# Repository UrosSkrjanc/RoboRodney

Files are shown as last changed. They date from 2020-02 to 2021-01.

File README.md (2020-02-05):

# RoboRodney

Zdravo.

Tuakj lahko snamete vse potrebno za izdelavo in sestavljanje robota.

V direktoriju Navodila so vsa navodila za sestavljanje, inštaliranje in uproabo robota. 

V direktoriju Nacrti co datoteke STL za tiskanje delov robota.

Direktorij roborodney pa vsebuje ROS paket za uproavljanje robota

uros.skrjanc@gmail.com

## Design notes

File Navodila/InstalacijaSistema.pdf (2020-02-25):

Kratek postopek inštalacije
1. Uvod
2. Formatiranje SD kartice, kopiranje sistema na kartico in namestitev sistema
3. Prijava uporabnika root kot glavnega uporabnika
4. Povezovanje uporabnika na robota
5. Nameščanje popravkov
6. SWAP datoteka
7. Dodajanje dodatnega I2C vodila
8. Nastavitve mreže
9. Inštalacija ROS
10. Inštalacija WiringPi
11. Prevajanje paketov
12. Preklapljanje med okenskim in terminalskim vmesnikom

### 1 – UVOD

Navodilo za inštalacijo se nanaša na operacijski sistem Ubuntu Mate 18.04 in ROS Melodic Morenia distribucijo. Pri ostalih operacijskih sistemih so podrobnosti lahko drugačne.

Programi za formatiranje in namestitev sistema na micro SD kartice delujeta na Windows operacijskih sistemih, PuTTY in FileZila pa tudi na nekaterih drugih operacijskih sistemih. Več informacij lahko dobite na straneh https://www.putty.org/ in https://filezilla-project.org/. Seveda se za terminalski dostop do robota in urejanje datotek lahko uporablja tudi druge programe, odvisno od operacijskega sistema, ki ga uporabljate na računalniku.

Sistem se nahaja na naslovu https://ubuntu-mate.org/download/, ROS distribucija pa na naslovu http://wiki.ros.org/melodic.

Za morebitne nejasnosti pri inštalaciji sem na voljo preko elektronske pošte: uros.skrjanc@gmail.com. V skladu s svojimi zmožnostmi in pristojnostmi bom skušal na vprašanja čim bolj jasno in enostavno odgovoriti.

### 2 – FORMATIRANJE SD KARTICE, KOPIRANJE SISTEMA NA KARTICO IN NAMESTITEV SISTEMA

Najprej s programom SD Card Formatter, ki ga dobimo na naslovu https://www.sdcard.org/downloads/formatter/, formatiramo micro SD kartico. Kapaciteta kartice naj bo najmanj 16GB, še bolje pa je, če je kapaciteta kartice 32GB. Nastavitve pri formatiranju kartice so privzete.

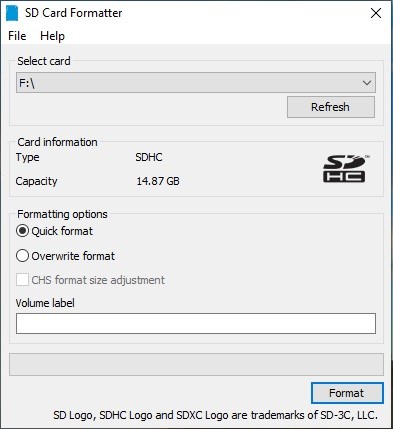
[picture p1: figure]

Z interneta prenesite sliko operacijskega sistema Ubuntu Mate 18.04.2. Ta se nahaja na https://ubuntu-mate.org/download/. Izberete verzijo za Raspberry Pi ARMv7.

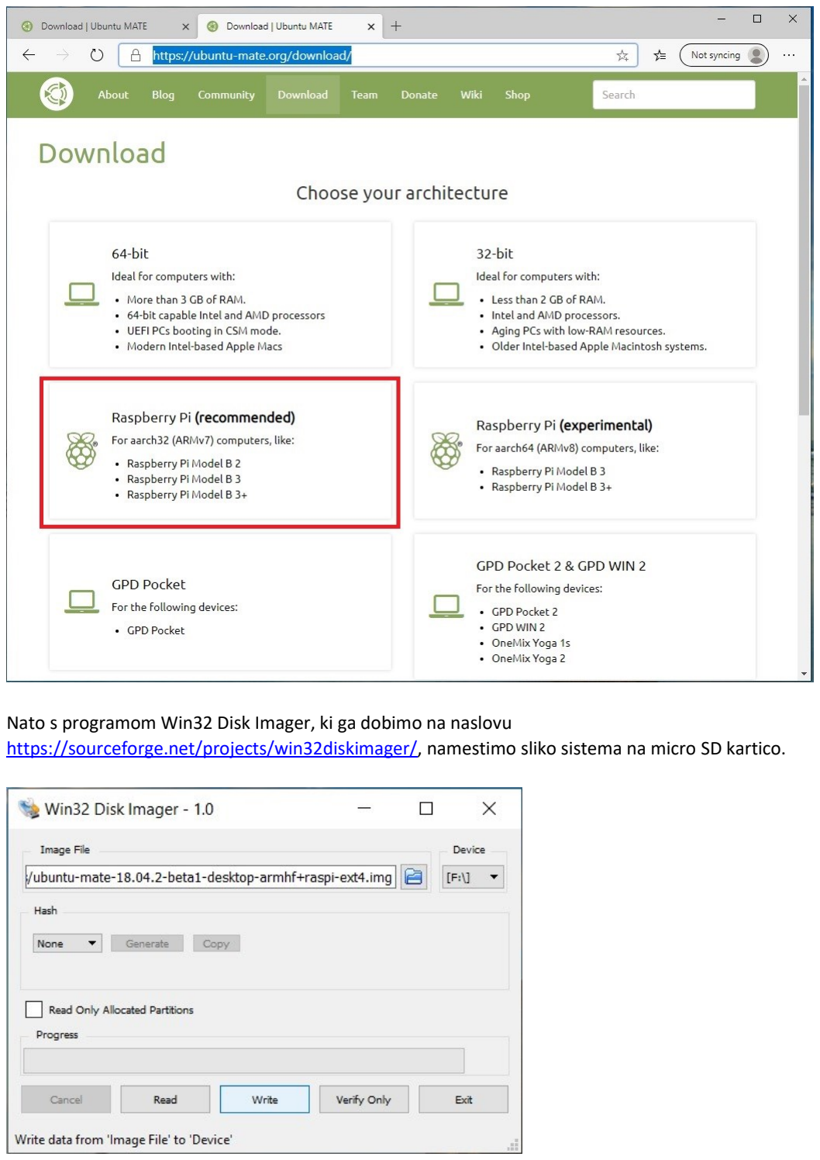
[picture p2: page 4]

Nato s programom Win32 Disk Imager, ki ga dobimo na naslovu https://sourceforge.net/projects/win32diskimager/, namestimo sliko sistema na micro SD kartico.

Inštalacija je preprosta, najbolje je, da je Raspberry računalnik z UTP kablom priklopljen na internet, tako da zazna datum, uro ter lokalne nastavitve. Glede na to, da je večina navodil za urejanje nastavitev operacijskega sistema na internetu napisana v angleščini, je za lažje delo najbolje, da osnovni jezik sistema ostane angleščina, tipkovnica pa se nastavi na slovensko.

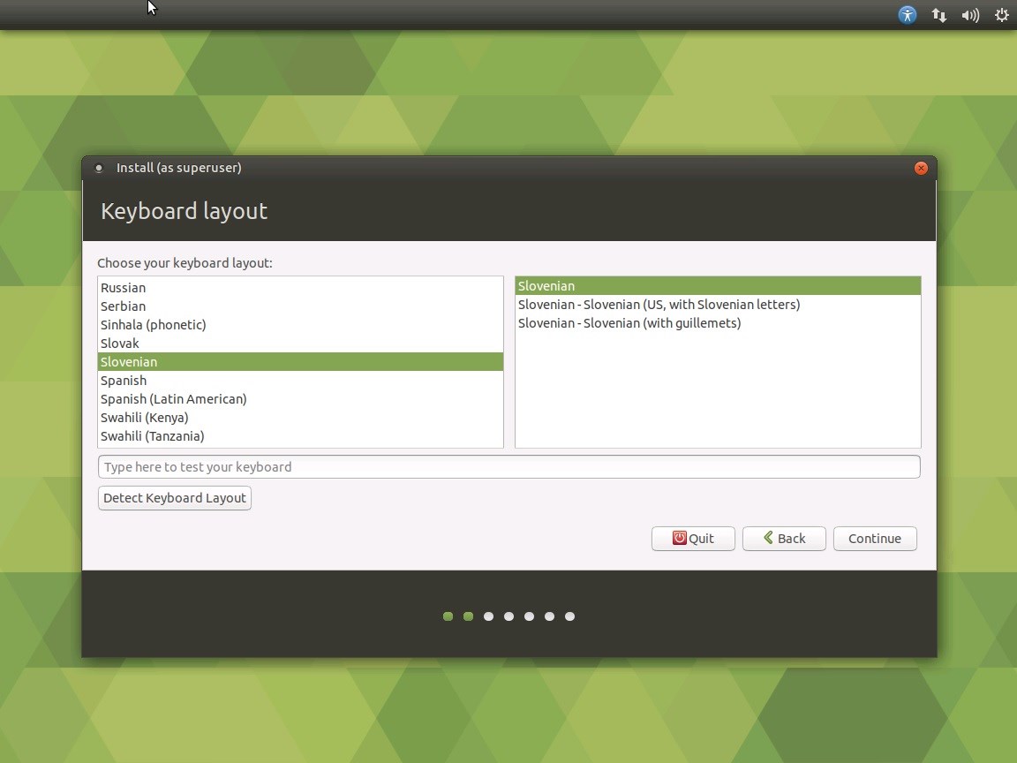
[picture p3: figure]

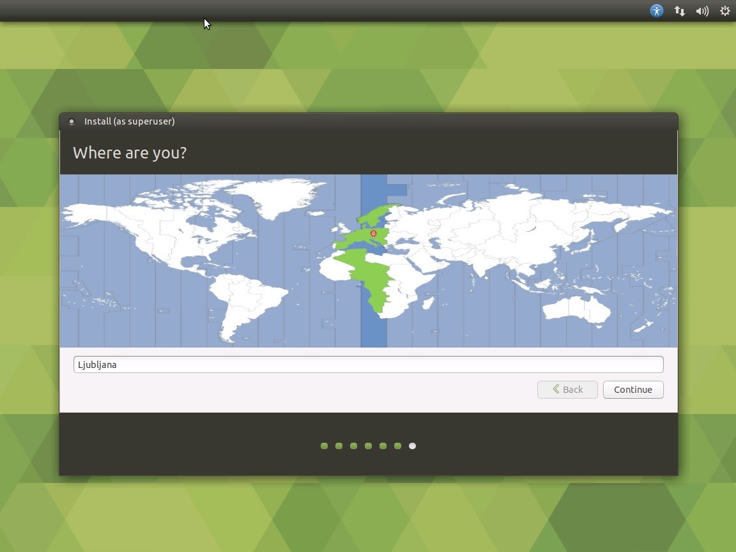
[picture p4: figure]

Uporabniško ime in geslo lahko izberete poljubno. Zaradi bolj enostavnega poganjanja je priporočljivo, da se uporabnik prijavi avtomatsko.

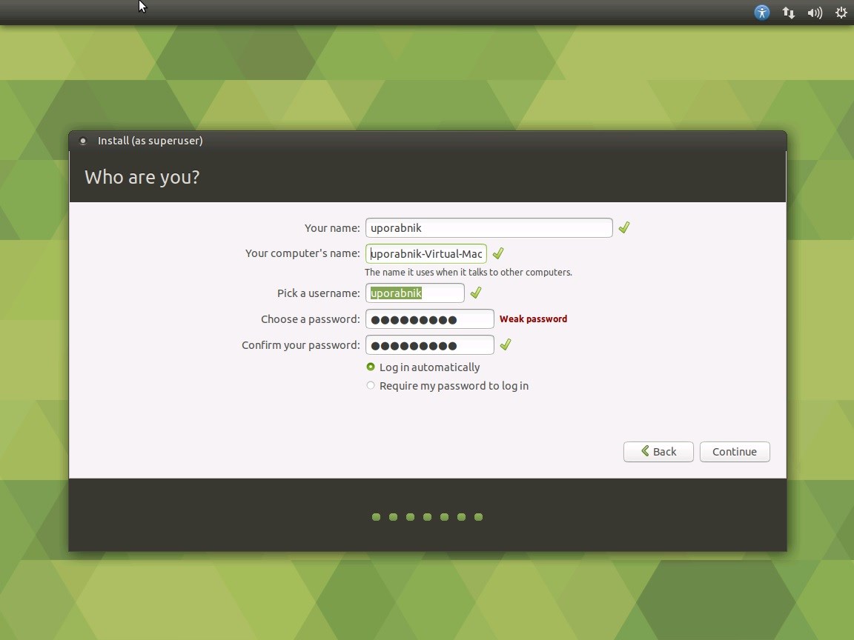
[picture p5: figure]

Ker SSH protokol na Ubuntu 18.04 ob inštalaciji ne deluje pravilno, je potrebna njegova ponovna namestitev. To naredimo tako, da odpremo terminalsko okno, v meniju (Menu – System tool – MATE Terminal) in poženemo naslednje ukaze:
sudo apt-get remove openssh-server
sudo apt-get purge openssh-server
sudo apt-get install openssh-server

Nato omogočimo še uporabo kamere in vodila I2C. To naredimo tako, da odpremo terminalsko okno v meniju (Menu – System tool – MATE Terminal) in poženemo program za konfiguracijo Raspberry računalnika.
Ukaz:
sudo raspi-config
Potem izberemo možnosti:
- Interfacing options – Camera – Yes
- Interfacing options – I2C – Yes

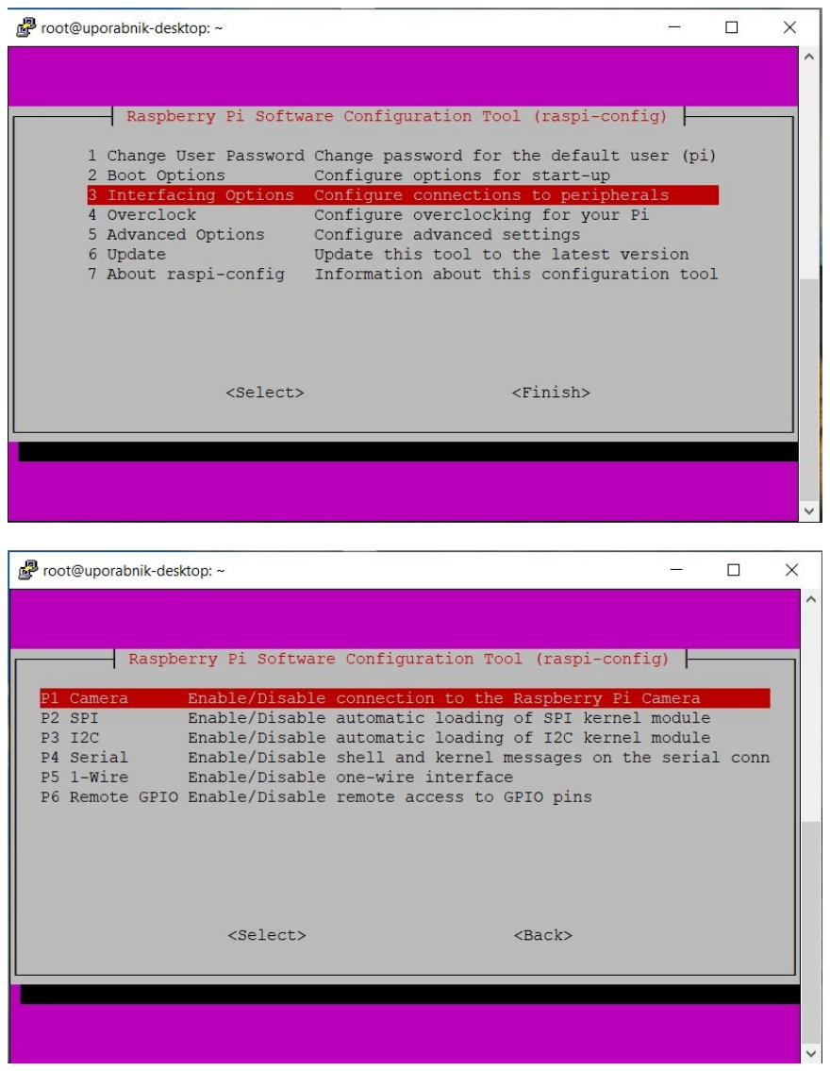
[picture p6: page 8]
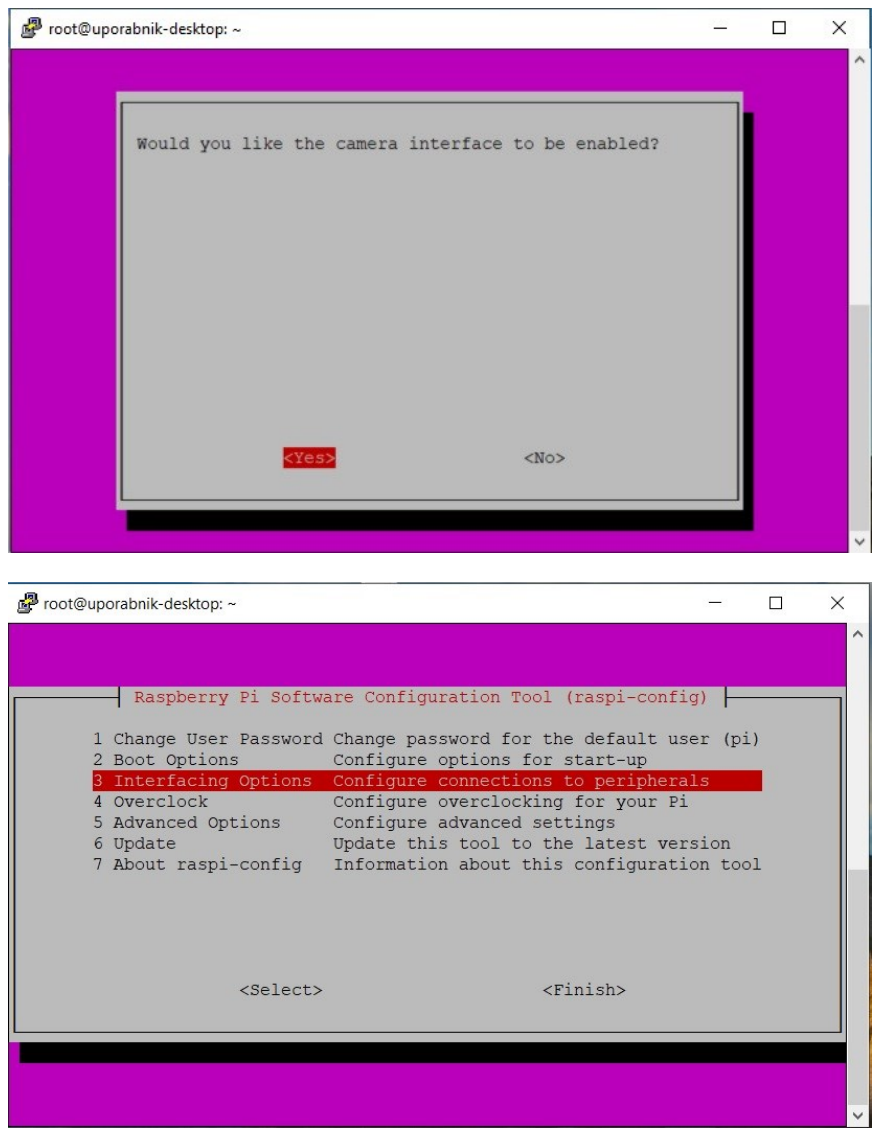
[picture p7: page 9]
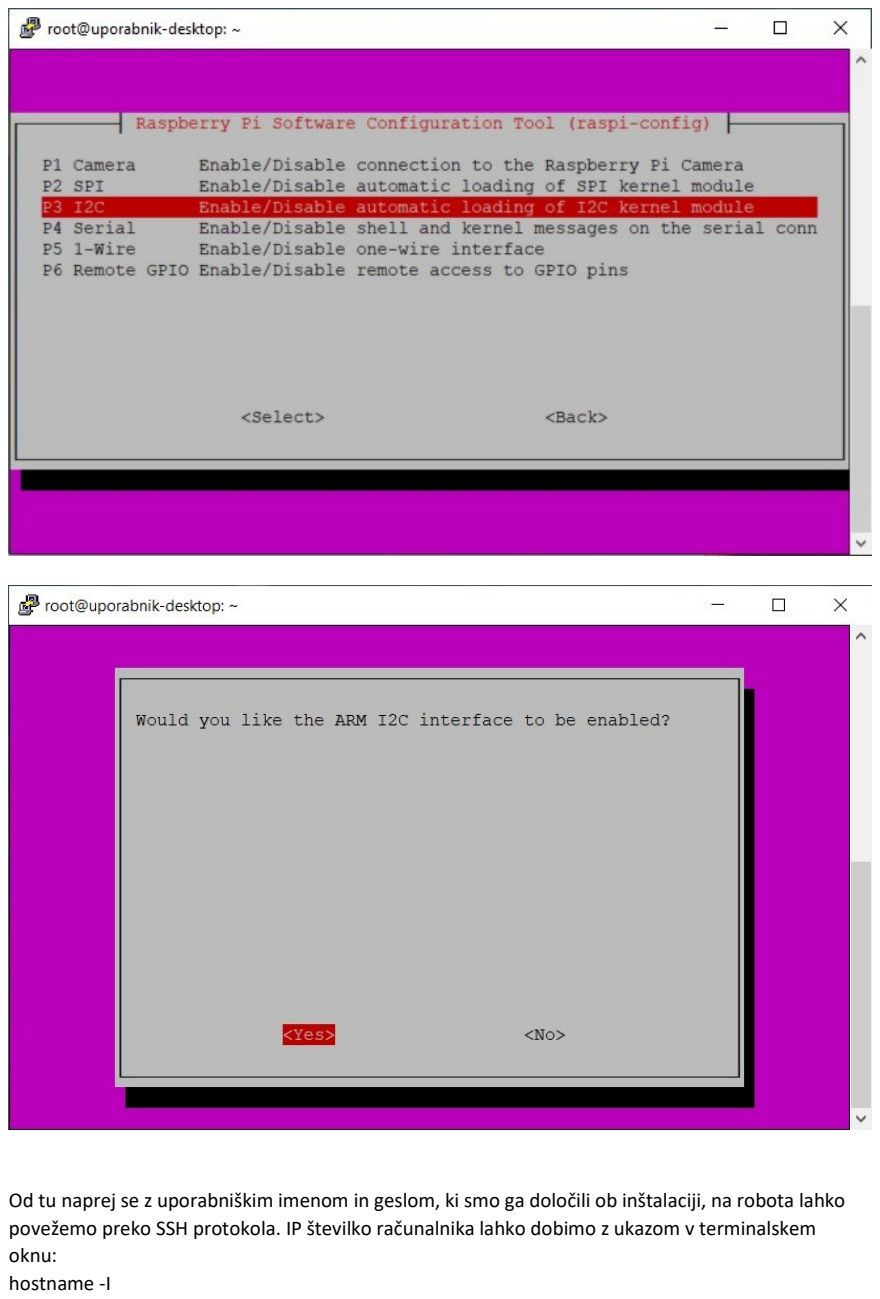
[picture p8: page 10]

Od tu naprej se z uporabniškim imenom in geslom, ki smo ga določili ob inštalaciji, na robota lahko povežemo preko SSH protokola. IP številko računalnika lahko dobimo z ukazom v terminalskem oknu:
hostname -I

Pred nadaljnjim delom je priporočljivo ponovno pognati robota. To lahko naredimo z ukazom v terminalskem oknu:
sudo shutdown -r now

### 3 - PRIJAVA UPORABNIKA ROOT KOT GLAVNEGA UPORABNIKA

Čeprav načeloma ni priporočljivo, da se uporabnik v računalnik prijavlja kot glavni administratorski račun, dostop do servo motorja zahteva prav to. Najprej moramo spremeniti geslo administratorskega računa. Poženemo ukaz za spremembo gesla, vpišemo najprej svoje geslo, potem pa dvakrat novo administratorsko geslo.
Ukaz:
sudo passwd root

Administratorskemu računu je potrebno dovoliti tudi logiranje preko SSH protokola. To dosežemo tako, da v datoteki /etc/ssh/sshd_config vrstico
# PermitRootLogin prohibit-password

spremenimo v
PermutRootLogin yes

Nato ponovno poženemo robota: sudo shutdown -r now

### 4 - POVEZOVANJE UPORABNIKA NA ROBOTA

Na robota se lahko povežem preko Putty programa z ukazno vrstico, datoteke pa lahko urejamo s programom FileZilla.

Programe lahko dobimo na naslovih:
Putty - https://www.putty.org/
FileZilla - https://filezilla-project.org/

Putty je namenjen povezavi preko SSH protokola na oddaljen računalnik in poganjanju ukazov v terminalskem načinu. Najprej na robotu z ukazom hostname -I preverim IP številko robota, potem odprem program in v okence vtipkam število, nakar program vpraša za uporabniško ime in geslo. Vpišemo uporabnika root in geslo, ki smo ga določili administratorskemu računu. Če so podatki vpisani pravilno in če je SSH dostop na robotu omogočen, potem se odpre terminal, preko katerega lahko krmilimo robota.

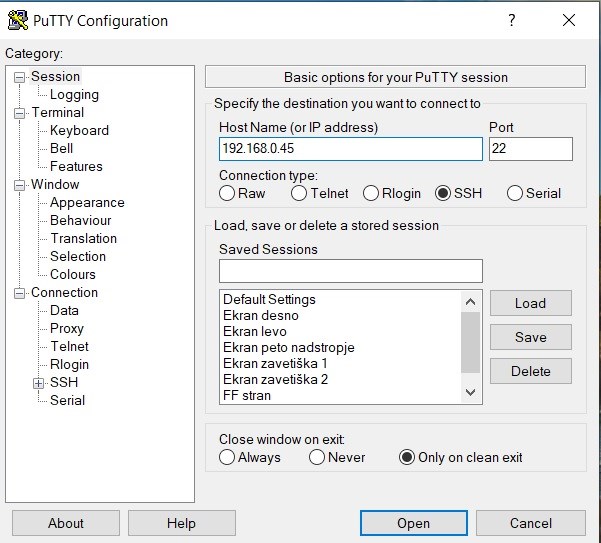
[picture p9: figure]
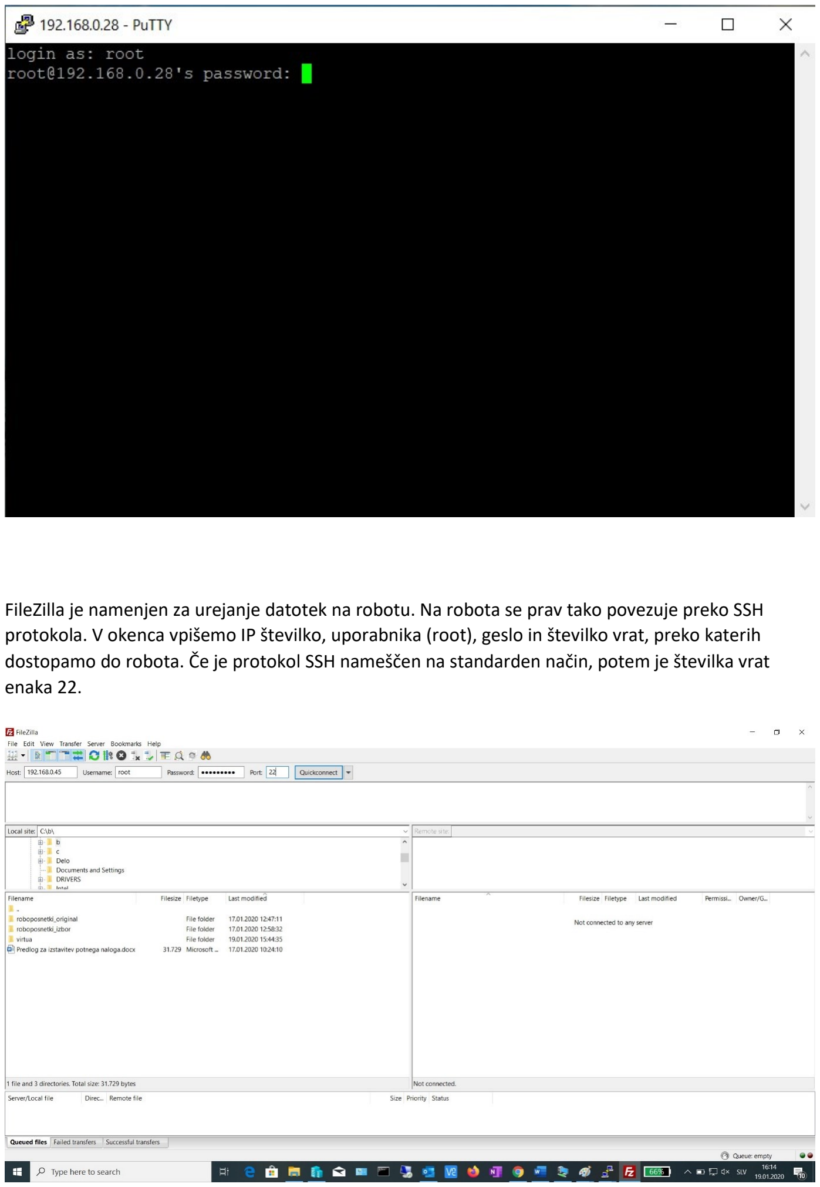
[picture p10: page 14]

FileZilla je namenjen za urejanje datotek na robotu. Na robota se prav tako povezuje preko SSH protokola. V okenca vpišemo IP številko, uporabnika (root), geslo in številko vrat, preko katerih dostopamo do robota. Če je protokol SSH nameščen na standarden način, potem je številka vrat enaka 22.

### 5 - NAMEŠČANJE POPRAVKOV

Na robota se preko SSH protokola povežem kot root uporabnik in izvedem naslednje ukaze apt-get update
apt-get upgrade

Včasih pri inštalaciji sistem opozori, da kakega nameščenega programa ne potrebuje več. V tem primeru poženemo ukaz za odstranitev teh programov:
apt-get autoremove

Naštete ukaze po potrebi izvedemo večkrat. Vsekakor tolikokrat, da so nameščeni vsi potrebni programi.

Pri inštalaciji sistema lahko pride do naslednje napake:
Errors were encountered while processing: /var/cache/apt/archives/linux-firmware-raspi2_1.20190819-0ubuntu0.18.04.1_armhf.deb

Za nadaljnjo inštalacijo je potrebno pognati ukaz:
dpkg -i --force-all /var/cache/apt/archives/linux-firmware-raspi2_1.20190819-0ubuntu0.18.04.1_armhf.deb

Samo ime datoteke, ki je ne more procesirati, se lahko razlikuje, tako da v ukazu uporabite ime datoteke, ki vam jo vrne.

Za pravilno delovanje robota moramo namestiti še:
knjižnico za I2C vodilo
apt-get install libi2c-dev
knjižnico zbar za zaznavanje QR kode:
apt-get install zbar-tools libzbar-dev libzbar0
knjižnico za komunikacijo z PS3 kompatibilno konzolo: apt-get install libusb-dev joystick python-pygame bluetooth in knjižnico za zajem slike s kamere v pythonu:
apt install python3-pip
pip3 install picamera

Da kamera na Ubuntu 18.04 deluje pravilno, je potrebno na koncu datoteke /etc/modules dodati vrstico bcm2835-v4l2.
Ukaz:
sudo echo bcm2835-v4l2 >> /etc/modules

### 6 - SWAP DATOTEKA

Pred namestitvijo ROS-a je priporočljivo narediti še swap datoteko. To naredimo z naslednjimi ukazi sudo fallocate -l 2G /swapfile
sudo chmod 600 /swapfile
sudo mkswap /swapfile
sudo swapon /swapfile
echo '/swapfile none swap sw 0 0' | sudo tee -a /etc/fstab

Če swap datoteka že obstaja in je premajhna, je potrebno najprej z datoteke /etc/fstab izbrisati vrstico, ki definira swap datoteko, potem pa izvesti zgoraj navedene korake.

Ukaz za odpiranje /etc/fstab datoteke:
sudo nano /etc/fstab

Zbrišemo vrstico
/swapfile | none | swap sw | 0 0

Nato ponovno zaženemo računalnik in izvedemo zgornje vrstice.

Če je swap datoteka pravilno kreirana, preverimo z ukazom free –m

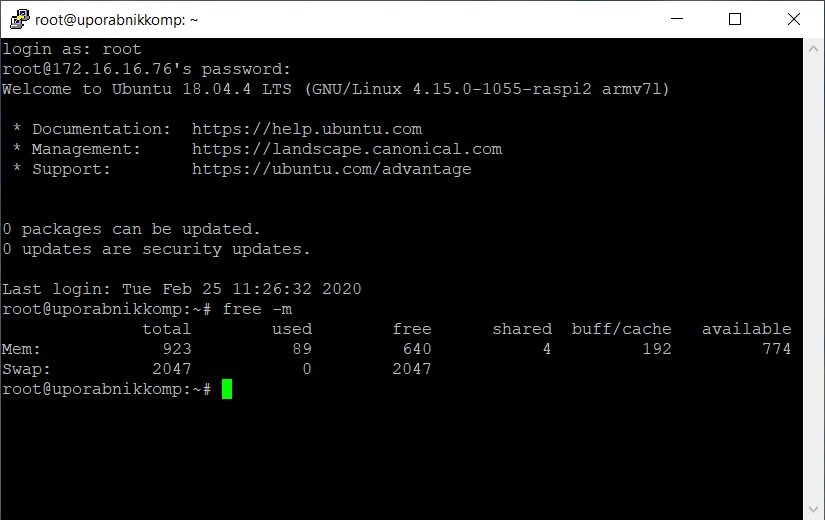
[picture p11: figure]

### 7 - DODAJANJE I2C VODILA

Pri komponentah, ki sem jih izbral za robota, imata laserski senzor VL53L0X in senzor za orientacijo v prostoru BNO055 isti naslov, zato je potrebno dati senzorja na različna I2C vodila. VL53L0X na robotu je nameščen na I2C številka 1, BNO055 pa na številki 3. Laser je na standardnem, privzetem vodilu oz. pinih (SDA-GPIO02, SCL-GPIO03), BNO055 pa je povezan s pini SDA-GPIO20, SCL-GPIO21. Zato moram v datoteko /boot/config.txt vpisati naslednjo vrstico: dtoverlay=i2c-gpio,bus=3,i2c_gpio_delay_us=1,i2c_gpio_sda=27,i2c_gpio_scl=22

Datoteko je potrebno spreminjati preko terminalskega okna. Spremembo izvedemo z ukazom: sudo echo dtoverlay=i2c-gpio,bus=3,i2c_gpio_delay_us=1,i2c_gpio_sda=27,i2c_gpio_scl=22 >> /boot/config.txt

Oznake pinov se nanašajo na spodnjo sliko:

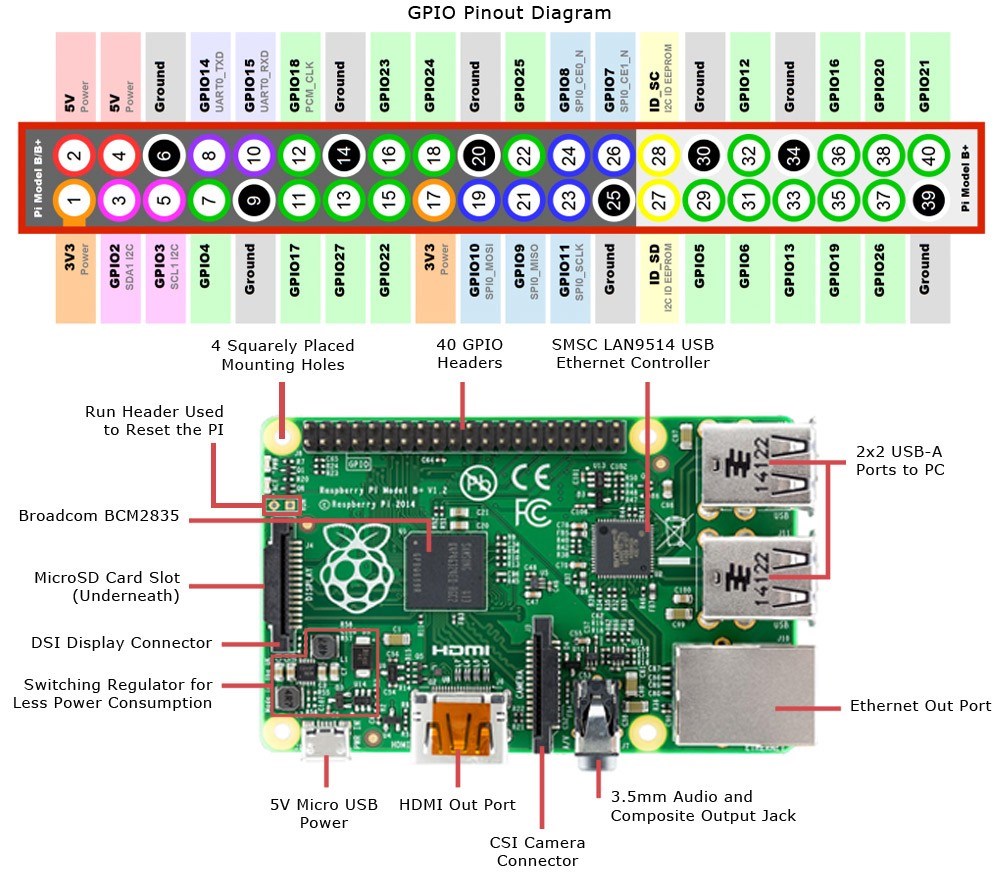
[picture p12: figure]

### 8 - NASTAVITVE MREŽE

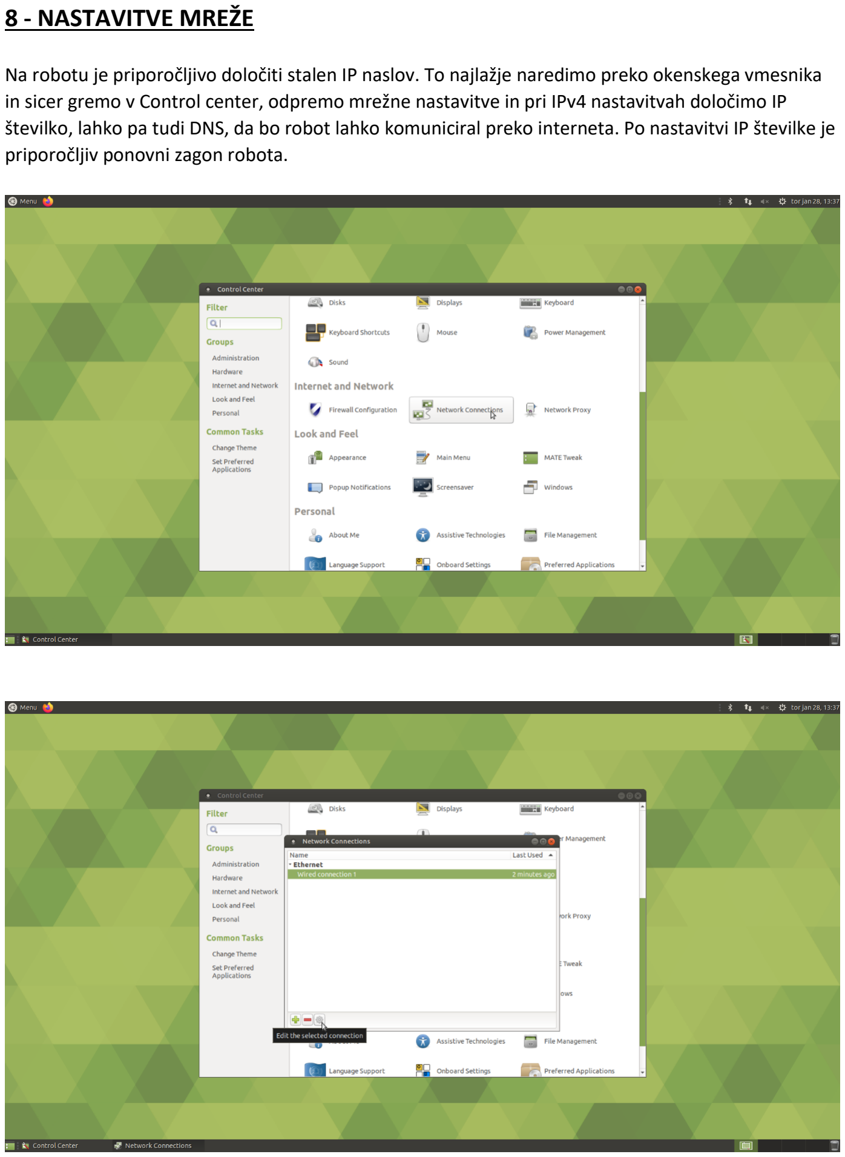
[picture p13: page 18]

Na robotu je priporočljivo določiti stalen IP naslov. To najlažje naredimo preko okenskega vmesnika in sicer gremo v Control center, odpremo mrežne nastavitve in pri IPv4 nastavitvah določimo IP številko, lahko pa tudi DNS, da bo robot lahko komuniciral preko interneta. Po nastavitvi IP številke je priporočljiv ponovni zagon robota.

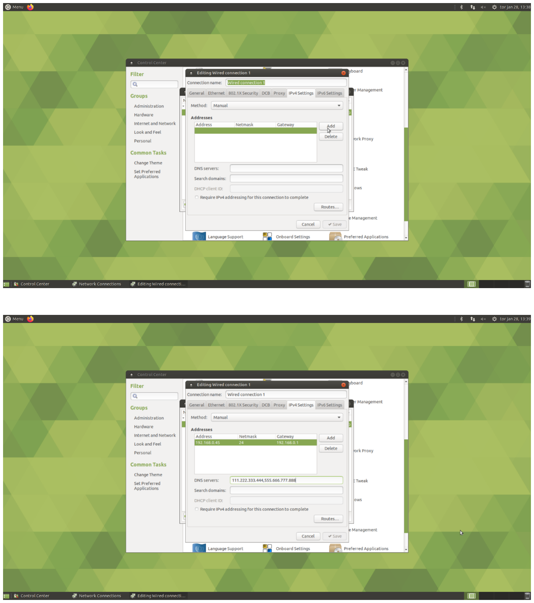
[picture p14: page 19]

### 9 - INŠTALACIJA ROS

Za prevajanje in poganjanje programov za nadzor robota je potrebno namestiti ROS distribucijo. Programi so preizkušeni na ROS Melodic Morenia distribuciji, z majhnimi popravki pa lahko delujejo tudi na drugih distribucijah.

Distribucija se nahaja na strani http://wiki.ros.org/Distributions.

Navodila za namestitev se nahajajo na strani http://wiki.ros.org/melodic/Installation/Ubuntu.

Ukazi za namestitev ROS Melodic Morenia:
sudo sh -c 'echo "deb http://packages.ros.org/ros/ubuntu $(lsb_release -sc) main" > /etc/apt/sources.list.d/ros-latest.list'
sudo apt-key adv --keyserver 'hkp://keyserver.ubuntu.com:80' --recv-key C1CF6E31E6BADE8868B172B4F42ED6FBAB17C654
sudo apt update
sudo apt install ros-melodic-desktop-full
sudo rosdep init
rosdep update
echo "source /opt/ros/melodic/setup.bash" >> ~/.bashrc
sudo apt install python-rosinstall python-rosinstall-generator python-wstool build-essential source ~/.bashrc

Potrebno je narediti še delovni prostor (workspace), v katerem bodo tekli programi. Namesto imena rosmelodic lahko izberete tudi kako drugo ime.

Ukazi za kreiranje delovnega prostora:
mkdir rosmelodic
cd rosmelodic
mkdir src
catkin_make

Nato v datoteko bashrc dodam vrstico source /root/rosmelodic/devel/setup.bash Ukaz:
echo "source /root/rosmelodic/devel/setup.bash " >> ~/.bashrc

Za delovanje PS3 kompatibilne konzole je potrebno namestiti tudi paket joy za ROS Ukaz:
apt-get install ros-melodic-joy
apt-get install ros-melodic-joystick-drivers

### 10 – INŠTALACIJA WIRINGIP

Za delovanje elektro motorjev je potrebno namestiti tudi knjižnico WiringPi. Navodila za namestitev se nahajajo na strani http://wiringpi.com/download-and-install/

Ko se povežete na robota preko terminalskega načina, izvedete naslednje ukaze:
git clone git://github.com/WiringPi/WiringPi.git
cd WiringPi
./build

Če pri prevajanju prihaja do napak, poskusite izvesti še naslednje korake: cd gpio
rm *.o
cd ..
./build

Knjižnico lahko prenesete na računalnik tudi z naslova https://github.com/WiringPi/WiringPi

### 11 – PREVAJANJE PAKETOV

Ko sta operacijski sistem in ROS distribucija uspešno nameščeni, je čas, da prenesete paket programov za robota, ga prevedete ter preizkusite delovanje robota.

Paket za navigacijo robota se nahaja na naslovu https://github.com/UrosSkrjanc/RoboRodney. Paket je v imeniku roborodney.

Najprej je potrebno programe prenesti v delovni prostor, ki smo ga kreirali v koraku 9. Preko terminalnega vmesnika se povežite na robota, nato pa izvedite naslednje ukaze:
git clone https://github.com/UrosSkrjanc/RoboRodney
cd RoboRodney
cp -r roborodney /root/rosmelodic/src

Nato se lahko lotite prevajanja paketov cd /root/rosmelodic
catkin_make

Samo prevajanje naj bi potekalo brez težav. Lahko se prikažejo določena opozorila, a na samo prevajanje programov in delovanje robota to ne vpliva. Ko se programi prevedejo pravilno, je robot pripravljen za uporabo.

### 12 – PREKLAPLJANJE MED OKENSKIM IN TERMINALSKIM VMESNIKOM

Ker ima računalnik Raspberry Pi 3B+ samo 1GB pomnilnika, bi lahko okenski vmesnik robotazaradi velike porabe pomnilnika pri delovanju oviral, zato je na koncu inštalacije in pred uporabo robota priporočljivo vklopiti zagon robota v terminalskem načinu. To storimo tako, da se na robota povežemo preko terminalskega okna in poženemo ukaz raspi-config. Izberemo možnost Boot options, nato možnost Desktop/CLI in Console Text console. Možnost potrdimo z OK. Ko izberemo izhod iz nastavitev, nas vpraša, če še enkrat zaženemo računalnik. Možnost izberemo in robot bi se moral zagnati v tekstovnem načinu.

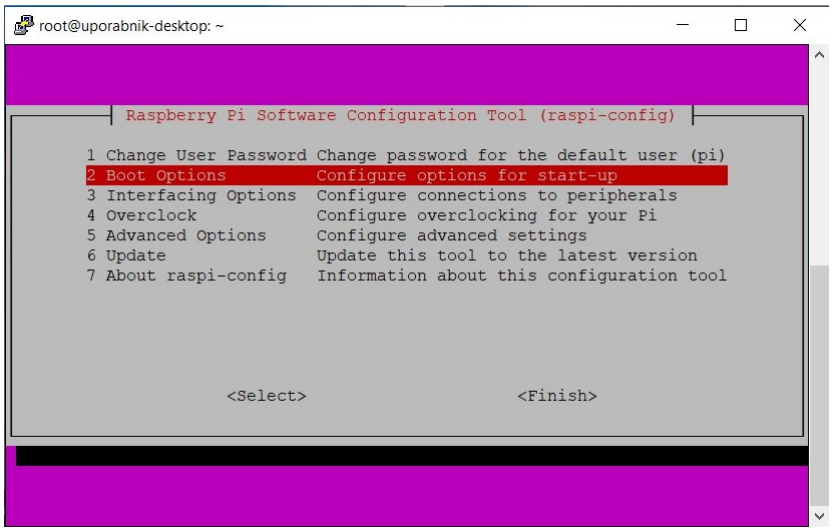
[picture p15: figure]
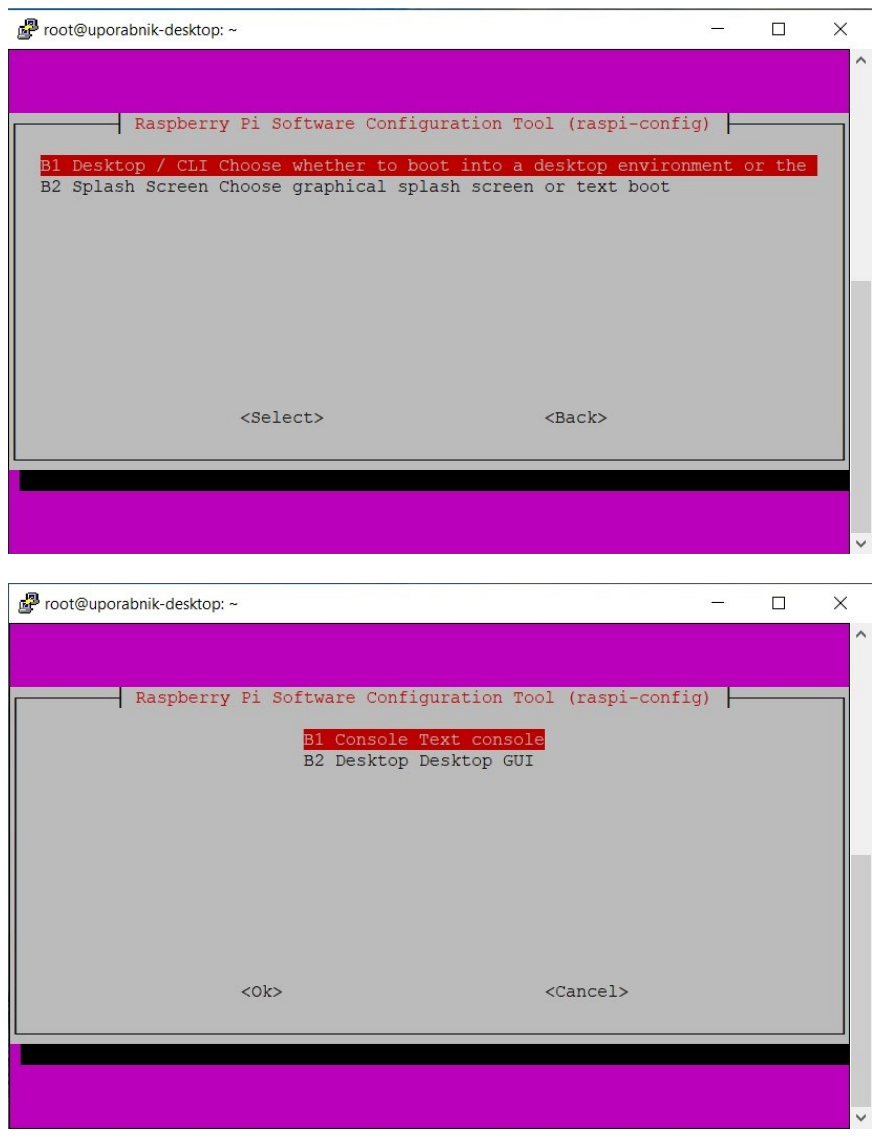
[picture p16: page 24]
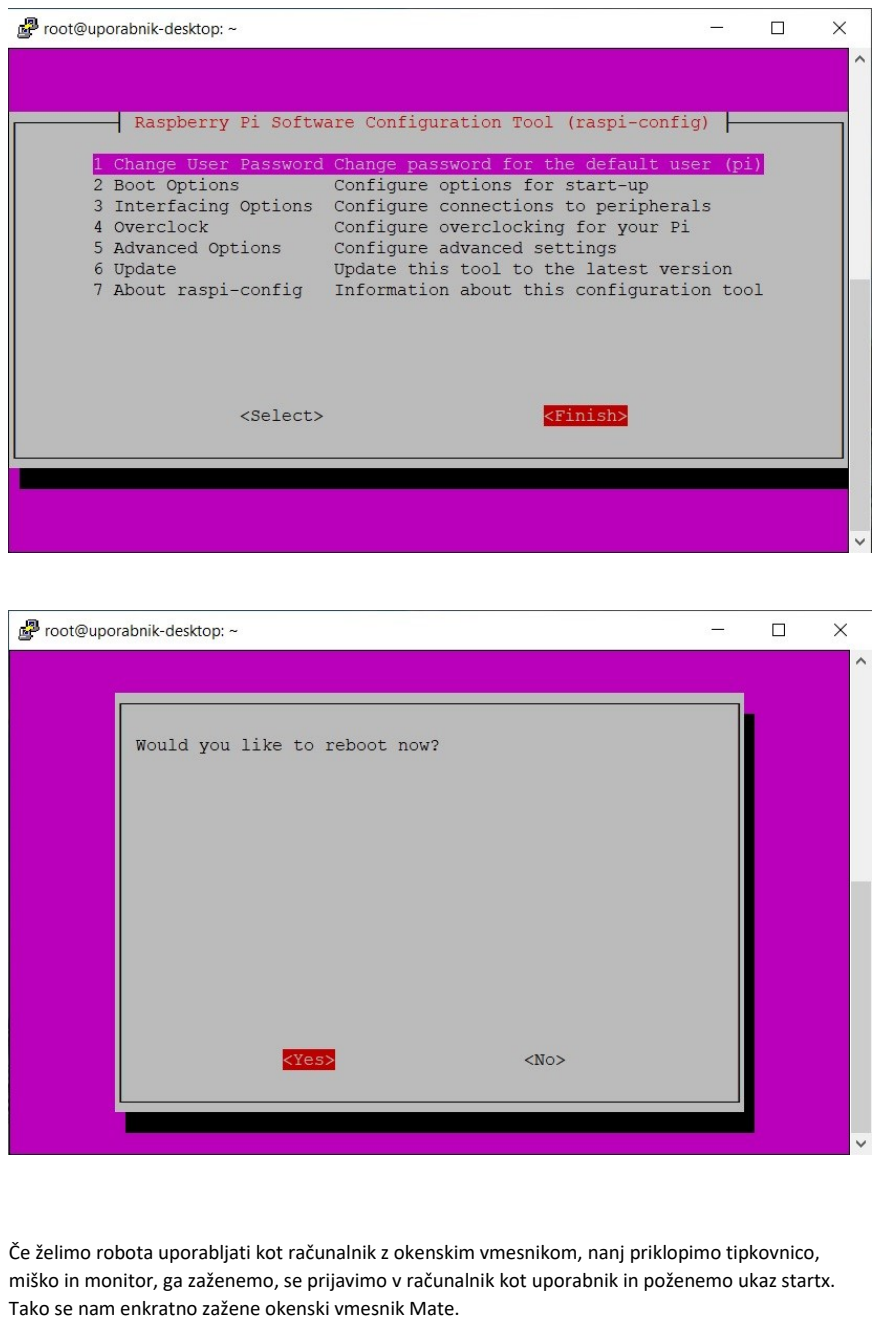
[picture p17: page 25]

Če želimo robota uporabljati kot računalnik z okenskim vmesnikom, nanj priklopimo tipkovnico, miško in monitor, ga zaženemo, se prijavimo v računalnik kot uporabnik in poženemo ukaz startx. Tako se nam enkratno zažene okenski vmesnik Mate.

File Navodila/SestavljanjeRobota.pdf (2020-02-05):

POTROŠNIKI ELEKTRIKE
Laser
Bno055
RTC (opcijsko)
Ultrasonic (opcijsko)
Servo motor

RPI ima 2x 5V in 2x3.3V
1x 5V je vhod z baterij
1x 5V je izhod na servo motor
Bi moral narediti kabel, ki ga priklopim na 3,3V izhod in GND, ima pa štiri izhode na naprave. Na obeh straneh je ženski priključek

Za robota potrebujem
Rdeč in bel kabel za ubec-RPI
5x rdeč in bel kanel za naprave, te kable zlotat za štiri naprave Rdeč in bel kabel za servo motor
Vsi napajalni kabli so M-Ž

Naprave na zgornji plasti (laser, ultrasonic, BNO055) bom napajal preko kabla, ki sem ga naredil iz več kablov
Za servo potegnem 5V kabel z RPI
RTC dobi napajanje z drugega 3.3V izhoda na RPI

SPODNJI DEL

Sestavni deli
- Plastično ohišje spodnji del
- Raspberry Pi 3B+
- Micro SD kattica 32GB
- Motor driver
- UBEC
- 4x motorji
- 4x kolesa
- Priključek za baterije
- 8 kablov moški-moški
- 4 kabli moški-ženska

Najprej na zgornjo stran ohišja z vijaki in maticami pričvrstim Raspberry Pi 3B+ in motor driver in sicer tako, da v vsako luknjo potisnem vijak, na vsak vijak potem dam dve matici, zato da RPI in motor driver nista direktno pričvrščena na plastiko, namestim RPI in motor driver na ohišje in ju spodaj pričvrstim z matico. Matice med RPI in plastiko ter med motor driver in plastiko dam zato, da se na dotika direktno plastike in da se ne segreva. Da ima zračenje.

SLIKA

Na motor driver priklopim UBEC in nastavek za baterije, potem pa z UBECA priklopim kabla na RPI, da ima napajanje. To naredim na 5V vhod in GND. Preizkusim še delovanje tako, da priklopim na RPI monitor, tipkovnico in miško ter poženem računalnik. Če se RPI postavi in deluje, so žice povezane pravilno. Rdeč kabel iz UBEC-a povežem na fizični pin 4, črni kabel oz. ozemljitev pa na fizični pin 6.

Postopek je tak, da vzamem M-Ž črn in bel kabel. Oba kabla na ženskem delu priklopim na UBEC, na moškem delu pa odstranim plastiko ter priklopim na motor-driver na vtiča 4(+) in 5(-), zraven teh kablov dam še prikjuček za baterije – rdeč je +, črn je -. Potem vzamem še črn in bel M-Ž kabel in moški del obeh kablov priklopim na UBEC, ženski pa na RPI in sicer bel kabel na fizični pin 4, črn kabel pa na fizični pin 6. Bel kabel je +, črn pa -.

Nato vzamem štiri motorje in osem kablov M-M. Kablom snamem plastično ohišje in rahlo zvijem pine, tako da se nekako zahaklajo na motor SLIKA!!! Potem pine kablov še bolj zvijem in spajkam kable na motor. Ko so žičke spajkane na motor, motorje namestim na ohišje, vsakega z dvema M3 30mm vijakoma in maticama, tako, da so vsi motorji na isti višini. Žičke potegnem skozi velike luknje ob straneh ohišja ter jih s spodnje strani potegnem do motor-driverja. Žičke naj bodo vsaka svoje barve, tako da jih je potem lažje priklopiti na motor-driver. Del žičke, ki ga namestim v motor driver, z izolirnim trakom izoliram, da se žičke nasprotnih polov ne dotikajo drug drugih. Plastiko z žičke snamem zato, ker je plastika prevelika in je težko pravilno namestiti žičke na motor driver.

SLIKE!!!!

Kable z motorjev potem potegnem skozi luknjo na sredini ohišja in jih namestim v motor driver.

Ko sem priklopil pine GPIO6, GPIO 13, GPIO 19 in GPIO 26, sta desna motorja pričela delovati takoj, ko sem priklopil baterije.

Motorji imajo + in – tako, kot je na sliki. To je pomembno zato, da pravilno priklopim kable na motor driver.

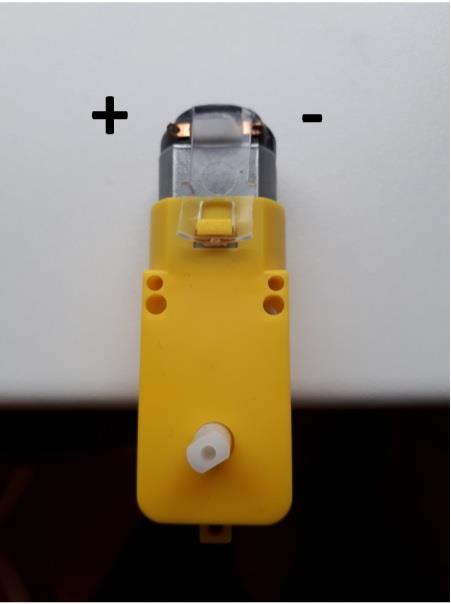
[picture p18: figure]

Pri motor driverju so pomembni tisti priklopi, ki so označeni z bold.

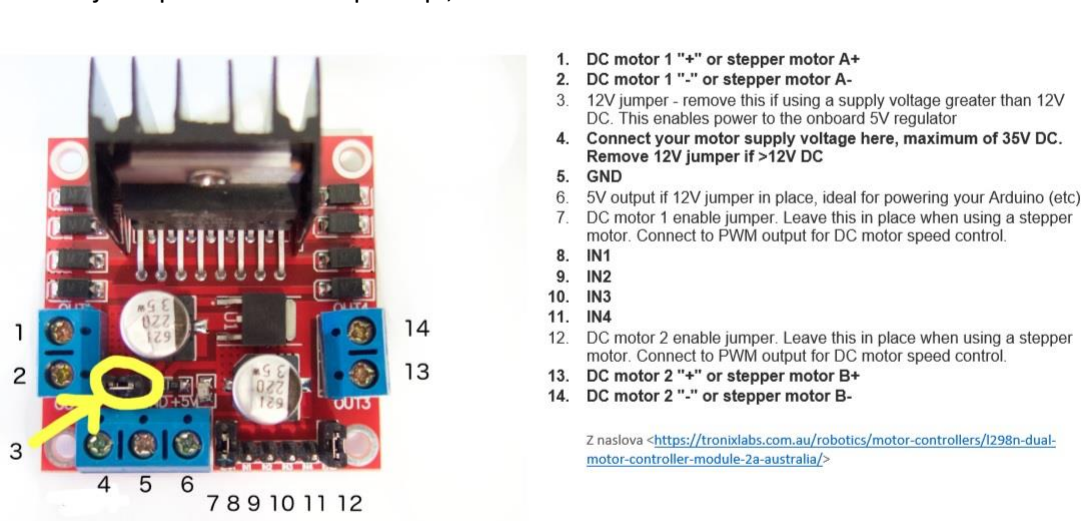
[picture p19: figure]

1,2 priklopimo motorja na levi strani. Na vsak priklop gresta dva kabla, tako da obema motorjema pošljemo signal naenkrat.
4,5 – napajanje z baterij in UBEC.
8,9,10,11 – kabli na RPI
13,14 – motorja na desni strani

SHEMA PRIKLOPA MOTORJEV NA MOTOR-DRIVER

Pozicija motorja | pol | barva žičke | Priklop na motor-driverju
Sprednji motor levo | + | Zelena | 1

Sprednji motor levo | - | Modra | 2
Sprednji motor desno | + | Rjava | 3
Sprednji motor levo | - | Rdeča | 4
Zadnji motor levo | + | Rumena | 1
Zadnji motor levo | - | Oranžna | 2
Zadnji motor desno | + | Siva | 3
Zadnji motor desno | - | Vijolična | 4

SHEMA PRIKLOPA MOTOR-DRIVER NA RPI

Barva | Izhod motor-driver | Gpio pin | Fizični pin na GPIO
Zelena | IN1 | GPIO 5 | 29
Modra | IN2 | GPIO 6 | 31
Vijolična | IN3 | GPIO 13 | 33
Siva | IN4 | GPIO 19 | 35

Ko so kabli povezani, poženem robota in preizkusim delovanje motorja z ukazi roscore
rosrun motor autodrive04
rosrun izogib auto08

t – naprej
b – nazaj
f – levo
h - desno

Motorje krmilimo tako, da za naprej pošljem vsem štirim motorjem signal za naprej, za nazaj pošljem vsem motorjem signal za nazaj, za levo pošljem levima motorjema signal za nazaj desnima za naprej, za desno levimo signal za naprej in desnima signal za nazaj. Tako se robot levo/desno vrti na mestu.

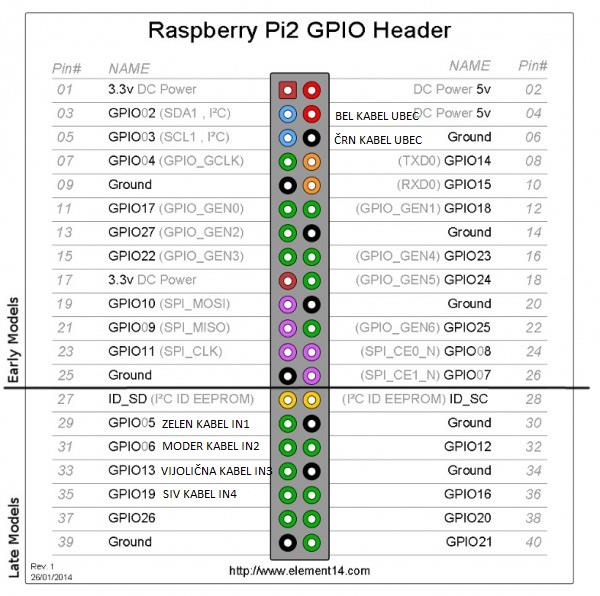
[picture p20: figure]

POTREBEN MATERIAL
- Spodnji del ohišja – 3D tisk
- 4x motorji
- 4x 3M 30mm vijaki za montažo motorjev
- 4x 3M matice za montažo motorjev
- 4x kolesa
- 8x raznobarvne kabli za priklop motorjev na motor-driver (zelena, modra, rjava, rdeča, rumena, oranžna, siva, vijolična)
- UBEC
- Motor driver
- 4x 3M 20mm vijaki za montažo motor-driverja
- 12 3M matice za montažo motor- driverja
- 2x M-Ž kabel za priklop motordriver – UBEC (črn, bel)
- 2x M-Ž kabel za priklop UBEC – RPI (črn, bel)
- Raspberry Pi 3B+

- 4x 3M 20mm vijaki za montažo RPI
- 12x 3M matice za montažo RPI
- Micro SD kartica 32GB
- 4x Ž-Ž raznobarvni kabli za priklop motor-driver – RPI (zelena, modra, vijolična, siva)

ZGORNJA PLAST

Sestavni deli
- Plastično ohišje zgornji del
- Nosilec za servo motor
- Nosilec za baterije
- Nosilna plošča za senzorje
- Nosilec za laser
- Nosilec za kamero
- Nosilec za ultrasonic
- Servo motor
- 4x 3M 10mm vijaki za montažo servo motorja
- 4x 3M matice za montažo servo motorja
- 2x M-Ž kabel za napajanje servo motorja
- 2x Ž-Ž kabel za upravljanje servo motorja
- Laser
- 2x 2,5M 10mm vijaki za montažo laserja na nosilec
- 2x 2,5M matice za montažo laserja na nosilec
- 2x 3M vijak za montažo laserja na robota
- 2x 3M matice za montažo laserja na robota
- 3x Ž-Ž kabel za priklop laserja
- Ultrasonic
- 4x Ž-Ž kabel za priklop ultrasonica
- 4x 3M 10mm vijaki za montažo ultrasonica
- 4x 3M matice za montažo ultrasonica
- RPI kamera
- Kabel za priklop RPI kamere
- 4x 3M 10mm vijaki za montažo kamere
- 4x 3M matice za montažo kamere
- RTC
- 4x Ž-Ž kabel za priklop RTC

Ko imam sestavljen spodnji del robota in ko sem prepričan, da pravilno deluje (delovanje računalnika, vožnja v vseh smereh), je na vrsti zgornji del. Najprej vzamem nosilca za servo motor in baterije ter jih pritrdim na zgornjo plast. Nosilec za baterije je lahko kjerkoli na robotu, vendar je najbolje, če ga damo na zadnjo stran robota. Nosilec za servo motor bi moral biti na sprednjem delu robota, in sicer naj ima režo, skozi katero damo kable servo motorja, obrnjeno naprej. Oba nosilca na robota pritrdimo z 3M 10mm dolgimi vijaki in maticami, na vsak nosilec 2 vijaka in 2 matici.

Nato zberemo kable in jih uredimo po barvah. Sistem, ki ga predlagam, je preprost. Rdeči kabli predstavljajo napajanje 3.3V, beli kabli predstavljajo napajanje 5V, črni kabli so ozemljitev, ostale barve pa so podatkovni kabli za naprave. Najbolje je vnaprej določiti, katere barve pripadajo posameznim napravam, tako da pri samem sestavljanju in poznejšem vzdrževanju ni težav.

PREDLOG BARV
Barva | pin | Fizični pin | Tip podatka
Vijolična | GPIO2 | 3 | SDA I2C 1

Siva | GPIO3 | 5 | SCL I2C 1
Oranžna | GPIO27 | 13 | SDA I2C 3
Rumena | GPIO22 | 15 | SCL I2C 3
Zelena | GPIO20 | 38 | Ultrasonic trigger
Modra | GPIO21 | 40 | Ultrasonic echo
Rjava | GPIO25 | 22 | Servo podatkovni kabel
Bela | 5V | 2 | Napajanje za servo motor
Črna | Ground | 20 | Ozemljitev za servo motor
Rdeča (1v 4 kabel) | 3V3 | 1 | Napajanje naprav
Črna (1 v 4 kabel) | Ground | 9 | Ozemljitev naprav

PRIKLOP SERVO MOTORJA
Potrebujem bel in črn M-Ž kabel za napajanje ter M-Ž kabel za krmiljenje motorja. Bel kabel z ženskim delom priklopim na fizični pin 1, črnega pa, ravno tako z ženskim delom, na fizični pin 20. Bel kabel napaja servo motor s 5V, črn kabel pa je ozemljitev. Tretji M-Ž kabel je namenjen krmiljenju servo motorja in ga priklopimo na GPIO25 oz. fizični pin 22. Moške dele kablov priklopimo na servo motor. Bel kabel gre v rdeč priključek, črn kabel gre v črn priključek in tretji kabel gre v rumen priključek. Če ima servo motor drugačne priključke, potem se kabli priklopijo na ustrezne priključke.

Za svojega robota uporabljam servo motor Hitec HS-322HD motor, ki je poceni in čisto dovolj vzdržljiv za robota. Več podrobnosti najdete na naslednjih povezavah. https://hitecrcd.com/products/servos/sport-servos/analog-sport-servos/hs-322hd/producthttps://www.servocity.com/hs-322hd-servohttps://servodatabase.com/servo/hitec/h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

NAPAJANJE NAPRAV NA ZGORNJEM DELU
Ker je naprav za napajanje več, kot je samih priključkov za 3,3V na RPI, je potrebno narediti dva kabla, enega za napajanje, drugega za ozemljitev, ki imata na enem koncu en ženski vhod, ki ga priklopimo na RPI, na drugem koncu pa štiri ženske izhode, ki jih priklopimo na naprave. To naredimo tako, da vzamemo 3 M-Ž kable in 1 Ž-Ž kabel rdeče barve. Vsem kablom M-Ž na moškem delu odstranimo plastiko, Ž-Ž kablu pa odstranimo plastiko na enem koncu. Potem olupljene oknce staknemo skupaj, tako da je na enem koncu en ženski vhod, na drugem koncu pa štirje ženski izhodi. Najbolje tako, da vzamemo en M-Ž in en Ž-Ž kabel, priključimo olupljena dela, ostale pa damo poleg in jih spajkamo. Na koncu jih še izoliramo z izolirnim trakom ter preizkusimo z multimetrom. Enak postopek ponovimo tudi s črnimi kabli. Tisti del rdečega kabla, ki ima ženski vhod, priklopimo na pin 3V3 (fizični pin 1), del črnega kabla, ki ima ženski vhod, pa priklopimo na pin Ground (fizični pin 9)

PRIKLOP LASERJA
Laser potrebujemo za merjenje razdalj. Čeprav je na robotu tudi ultrasonic, je laser natančnejši za merjenje razdalj, v kombinaciji s servo motorjem pa lahko naredimo tudi preprost LIDAR, ki se sicer počasnejši in manj natančen od običajnih LIDAR-jev, je pa precej cenejši in je dovolj primeren za spoznavanje osnovnih principov.
Za priklop potrebujemo 2 Ž-Ž kabla in sicer vijoličnega in sivega. Vijoličnega priklopimo na pin GPIO2 oz. fizični pin 3, sivega pa na pin GPIO3 oz. fizični pin 5.

PRIKLOP ULTRASONICA

Ultrasonic nam služi za zaznavanje razdalj pred robotom. Za zaznavanje razdalj robot sicer največ uporablja laser, vendar je vmesnik za ultrasonic ravno tako sprogramiran, tako da si lahko
pomagamo tudi z njim.
Za priklop potrebujemo 2 Ž-Ž kabla in sicer zelenega in modrega. Zelenega priklopimo na pin GPIO20 oz fizični pin 38, modrega pa na pin GPIO21 oz. fizični pin 40. Zelen kabel služi ultrasonicu za trigger moder pa za echo.

PRIKLOP BNO055
Senzor BNO055 potrebujemo za orientacijo v prostoru. Za sedaj ga robot uporablja samo za kontrolo kota v prostoru. Ko robot zažene senzor, ima vrednost 0, potem pa lahko preberemo s senzorja trenutni kot glede na začetni kot. Uporabljamo za samo navigacijo v prostoru.
Za priklop potrebujem 2 Ž-Ž kabla in sicer oranžnega in rumenega. Oranžnega priklopim na pin GPIO27 oz. fizični pin 13. rumenega pa na pin GPIO22 oz. fizični pin 15.
Ker imata laser in BNO055 lahko, vsaj v mojem primeru, isti naslov, jih je potrebno priklopiti na različne I2C vmesnike. Več I2C vmesnikov določimo v datoteki /boot/config.txt po navodilih https://www.instructables.com/id/Raspberry-PI-Multiple-I2c-Devices/

PRIKLOP KAMERE
Na žalost je kabel, ki ga dobimo poleg kamere, prekratek, da bi ga lahko uporabili z robotom, zato je potrebno naročiti daljši kabel. Na svojem robotu uporabljam 610mm dolg kabel, ki ga priklopim ravno tako, kot krajšega. Kabel priklopim na poseben I/O za kamero, potrebno pa je paziti tudi na to, da je podatkovni kabel za kamero pravilno obrnjen, da slučajno ne poškodujete kamere. https://thepihut.com/blogs/raspberry-pi-tutorials/16021420-how-to-install-use-the-raspberry-pi-camera (https://thepihut.com/blogs/raspberry-pi-tutorials/16021420-how-to-install-use-the-raspberry-pi-camera)

Ko imamo priklopljene kable na GPIO in podatkovni kabel za kamero, vzamemo zgornji del in vse kable potegnemo skozi sredinsko luknjo in zgornji del robota nataknemo na spodnji del robota toliko, da se nožice zgornjega dela zataknejo v spodnji del. Dobro je, da je površina zgornjega dela robota ravna, tako da, če je na nožicah ostalo kaj nepotrebne plastike, le to odstranimo.

Kable, ki smo jih potegnili skozi osrednjo luknjo na zgornjem delu robota, lahko tudi primerno označimo ali pa skupine kablov, na primer, kable ki jih priklopimo na posamezno napravo, zvežemo skupaj z vezicami ali kako drugače. Sam sem se odločil, da vzamem posebne plastične tube in na takšen način ločim kable med sabo in jih do neke mere tudi zaščitim.

Tako moramo po tej fazi imeti na zgornji strani:
- Priklop za baterije
- Podatkovni kabel za RPI kamero
- Napajalna in podatkovni kabel a servo motor (rdeč, črn, zelen in moder kabel)
- Napajalna in podatkovna kabla za laser (rdeč, črn, vijoličen in siv kabel
- Napajalna in podatkovna kabla na BNO05 (rdeč, črn, oranžen in rumen kabel)

Ko imamo zgornji del nameščen na robotu, vzamemo servo motor in ga damo v nosilec tako, da gredo kabli motorja skozi vzdolžno režo nosilca. Na zadnjem delu ga nato pričvrstimo z dvema 3M 10mm dolgima vijakoma in maticama, tako da je raven. Kable servo motorja potem potegnemo nazaj in jih priklopimo na ustrezna kable, ki smo jih potegnili s spodnjega dela. Bel kabel priklopimo na rdeč vhod, črn kabel na črn vhod in rjav na rumen vhod. Kabel potem še uredimo, najbolj z vezico, tako da ne motijo delovanja robota.
Nato prižgemo robota, poženemo program, s katerim postavimo motor v sredino …. in robota potem ugasnemo.

Potem vzamemo nosilec za senzorje in nanj namestimo nosilce za ultrasonic, kamero in laser. Najbolje je, zaradi preproste uporabe, laser namestiti na sredino, potem pa levo in desno namestimo ultrasonic in kamero. Kaj je na levi in kaj na desni strani ni ravno pomembno. Nosilce za vse tri naprave pritrdimo na ploščo z dvema 3M 10mm vijakoma in maticama za vsak nosilec. Nosilca za ultrasonic in laser sta sestavljena iz enega dela, tako da potem vzamemo ultrasonic in ga s pini navzgor potisnemo skozi luknji na nosilcu. Potem dva 2,5M vijaka, jih potisnemo skozi luknje na nosilcu za laser tako, da je glava usmerjena naprej, na vsak vijak damo plastičen distančnik, da vijaki ne povzročajo kratkega sitka, nataknemo laser, potem še en plastični distančnik na vsak vijak in vse skupaj fiksiramo z dvema 2,5M maticama.

Nosilec za kamero je sestavljen iz dve delov. Sprednji del smo namestili na ploščo za senzorje. Na zadnji del potem namestimo kamero s kablom in sicer tako, da podatkovni kabel zakamero gleda navzgor. Potem namestimo zadnji del nosilca na sprednji del in sicer tako, da je podatkovni kabel za kamero gleda navzgor. Skozi luknji na sprednji strani namestimo še dva vijaka 3M 10mm in jih utrdimo z maticama 3M.

Ko imamo senzorje nameščene na plošči za senzorje, ploščo namestimo na servo motor tako, da križni nastavek na motorju namestimo na vodila na spodnji strani plošče.

Senozor BNO055 na žalost nima lukenj, da bi ga lahko pritrdili na zgornji del robota, zato lahko vzamemo vezico in za pritrdimo na zgornji del robota.

V tej fazi bi morali imeti sestavljen robot. Če so kabli še neurejeni, jih lahko z nekaj vezicami uredite, tako da ne motijo vožnje robota. Pomembno je tudi, da so kabli dovolj dolgi, da se plošča s senzorji lahko ustrezno vrti levo desno vsaj 90 stopinj v vsako smer. Kable lahko potegnete tudi skozi luknji na zadnji strani plošče za senzorje

Nato vzamemo nosilec za servo motor

Potem vzamemo servo motor, priklopimo kabl

Preden sestavim zgornji del, priklopim vse potrebne kable za senzorje na RPI in jih primerno označim. Ko so priklopljeni, vzamem zgornji del, nanj z vijaki pričvrstim nosilec za baterije in nosilec za servo motor. Nato dam v nosilec za servo motor servo motor. Nato vzamem nosilno ploščo za senzorje, nanjo pričvrstim laser in kamero, lahko tudi ultrasonic. Potem vzamem zgornji del, ga namestim na robota, potegnem skozi luknjo kable.

Najprej povežem servo motor, prižgem robota in kalibriram servo motor oz. postavim v srednjo pozicijo. Robota ugasnem, namestim bel križen nosilec na motor, na motor namestim plošči ter jo pričvrstim z vijakom na motor.

Potem povežem komponente s kabli in preizkusim robota.

MATERIAL ZA ROBOTA – BREZ ULTRASONICA
- Ohišje
- Spodnji del robota
- Zgornji del robota
- Nosilec za baterije
- Nosilec za servo motor
- Nosilna plošča za senzorje
- Nosilec za laser
- Nosilec za kamero
- 4x motorji
- 4x kolesa
- 8x kabli za povezavo motorjev na motor-driver
- UBEC
- 2x M-Ž kabla za povezavo UBECa na motor-driver
- 2x Ž-Ž kabla za povezavo UBECa na RPI
- 4x Ž-Ž kabli za povezavo motor-driver na RPI
- 8x 3M 30mm vijaki + 8 matic 3M za motorje
- 4x 3M 20mm vijaki + 12 matic 3M za motor-driver
- 4x3M 20mm vijaki + 12 matic 3M za RPI
- Motor-driver
- RPI 3B+
- BNO055
- RTC
- Laser
- RPI kamera
- Kabel za RPI kamero 610mm
- Servo motor
- 4x Ž-Ž kabel za laser
- 4x Ž-Ž kabel za BNO055

- 3x M-Ž kabel za servo motor
- 4x Ž-Ž kabel za RTC
- Baterije

PREDVIDENA NABAVA ZA NOVEGA ROBOTA

- Ohišje
- Spodnji del robota
- Zgornji del robota
- Nosilec za baterije
- Nosilec za servo motor
- Nosilna plošča za senzorje
- Nosilec za laser
- Nosilec za kamero
- 4x motorji
- 4x kolesa
- 8x kabli za povezavo motorjev na motor-driver
- UBEC
- 2x M-Ž kabla za povezavo UBECa na motor-driver
- 2x Ž-Ž kabla za povezavo UBECa na RPI
- 4x Ž-Ž kabli za povezavo motor-driver na RPI
- 8x 3M 30mm vijaki + 8 matic 3M za motorje
- 4x 3M 20mm vijaki + 12 matic 3M za motor-driver
- 4x3M 20mm vijaki + 12 matic 3M za RPI
- Motor-driver
- RPI 3B+
- BNO055 (naročeno)
- 2x vijaki – še pogedat
- RTC
- 3x 2,5M 10mm vijaki + matice
- Laser
- 2x3M 10mm vijaki in matici, 2+2,5M 10mm vijaki + matici
- RPI kamera
- 4x3M 10mm vijaki + matice
- Kabel za RPI kamero 610mm
- Servo motor
- 4x Ž-Ž kabel za laser
- 4x Ž-Ž kabel za BNO055
- 3x M-Ž kabel za servo motor
- 4x Ž-Ž kabel za RTC
- Baterije

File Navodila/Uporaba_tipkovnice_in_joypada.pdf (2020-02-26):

NAVODILA ZA VOŽNJO ROBOTA S POMOČJO TIPKOVNICE, PS3 KOMPATIBILNE KONZOLE ALI SAMOSTOJNE VOŽNJE ROBOTA

Če smo uspešno namestili sistem in prevedli programe, naj bi bil robot pripravljen za uporabo. Sam robot lahko deluje v enem izmed treh načinov:
1. vožnja robota s pomočjo tipkovnice namiznega ali prenosnega računalnika
2. vožnja robota s pomočjo PS3 kompatibilne konzole
3. samostojna vožnja robota.

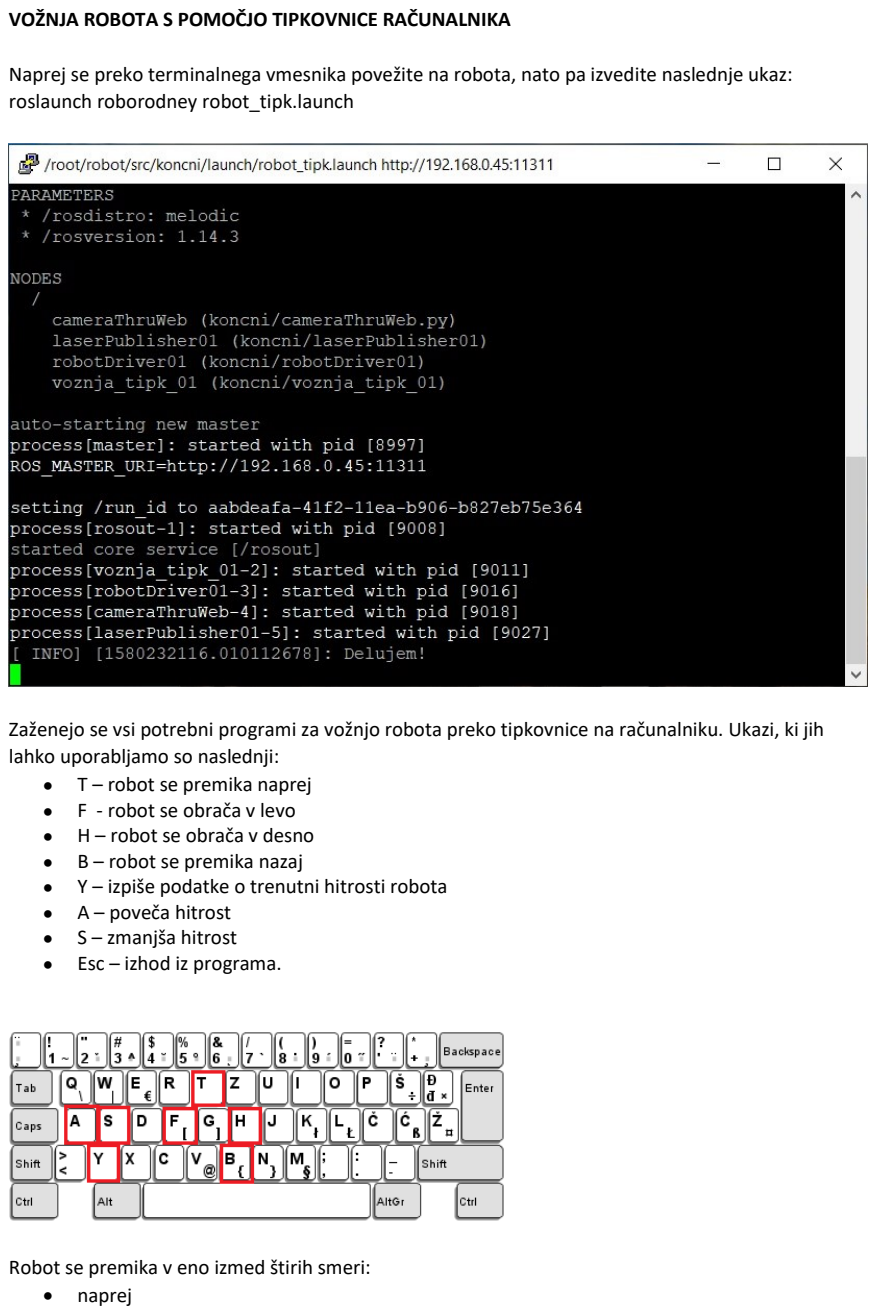
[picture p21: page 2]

VOŽNJA ROBOTA S POMOČJO TIPKOVNICE RAČUNALNIKA

Naprej se preko terminalnega vmesnika povežite na robota, nato pa izvedite naslednje ukaz: roslaunch roborodney robot_tipk.launch

Zaženejo se vsi potrebni programi za vožnjo robota preko tipkovnice na računalniku. Ukazi, ki jih lahko uporabljamo so naslednji:
- T – robot se premika naprej
- F - robot se obrača v levo
- H – robot se obrača v desno
- B – robot se premika nazaj
- Y – izpiše podatke o trenutni hitrosti robota
- A – poveča hitrost
- S – zmanjša hitrost
- Esc – izhod iz programa.

Robot se premika v eno izmed štirih smeri:
- naprej

- nazaj
- levo
- desno.

Robot ne more kombinirati več ukazov naenkrat, tako da uporabljamo lahko samo eno tipko naenkrat. Dokler držimo tipko, robot izvaja premikanje v določeni smeri, ko tipko spustimo, se robot ustavi. Če se robot približa oviri na razdaljo, manjšo od 50 cm, opozori na bližino ovire, a same vožnje ne ustavi.

Če v spletni brskalnik vpišemo naslov http://IP_STEVILKA_ROBOTA:8000, potem lahko spremljamo sliko s kamere na robotu. IP številko smo določili v točki 8.

Sama kvaliteta prenosa slike je odvisna od zmogljivosti brezžične povezave, pomembno je, da je robot v dosegu brezžičnega omrežja, drugače ga ne moremo upravljati. Robot se v tem primeru ne bo premikal samodejno, zato ga bo potrebno ročno prestaviti na primernejši prostor znotraj dosega signala brezžičnega omrežja.

VOŽNJA S POMOČJO PS3 KOMPATIBILNE KONZOLE

Robota lahko na enak način, kot s pomočjo tipkovnice, upravljamo tudi s pomočjo PS3 kompatibilne konzole. Za povezavo robota in konzole je najbolj smiselno uporabiti bluetooth povezavo, ki je na Raspberry Pi 3B+ vključena in je ni potrebno posebej nameščati. Dovoljevala naj bi upravljanje na razdalji okrog 10 metrov, vendar je razdalja precej odvisna tudi od samega terena, po katerem vozimo robota.

Naprej, nazaj, levo in desno upravljamo robota z levo stranjo konzole, na desni pa uravnavamo hitrost robota, informacije o hitrosti in izhod iz programa.

Naprej se preko terminalnega vmesnika povežite na robota, nato pa izvedite naslednji ukaz: roslaunch roborodney robot_joy.launch

Robota upravljamo s tipkami, označenimi na sliki:
1. robot se premika naprej
2. robot se premika nazaj
3. robot se obrača v levo
4. robot se obrača v desno
5. poveča hitrosti robota
6. zmanjša hitrosti robota
7. izhod iz programa
8. izpiše podatke o trenutni hitrosti robota.

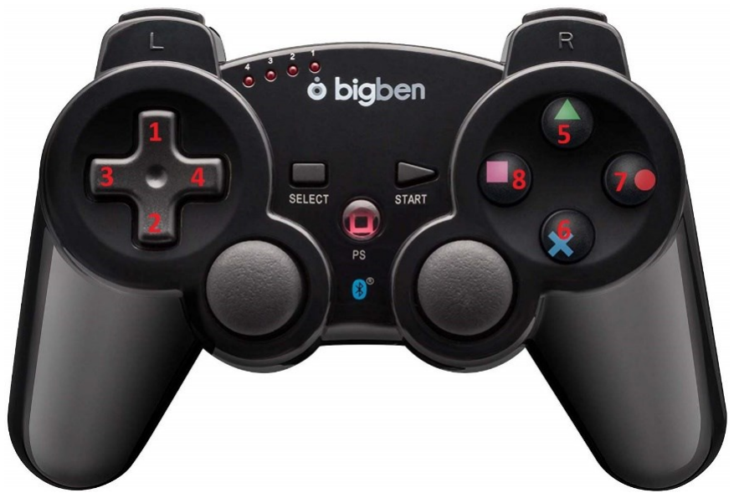
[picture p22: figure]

Program deluje tako, da dokler držimo posamezno tipko na konzoli, se robot premika ali obrača v želeno smer. Ko tipko spustimo, se robot ustavi.

POSTOPEK INŠTALACIJE PS3 KOMPATIBILNE KONZOLE NA ROBOTA

Za uporabo PS3 kompatibilne konzole je potrebno narediti nekaj korakov, da seznanimo konzolo in robota, ter da robot tudi v bodoče dovoli povezavo s konzolo.

Najprej je potrebno namestiti vse potrebne knjižnice z ukazom, kar smo sicer že naredili v navodilih za inštalacijo sistema pri točki 5:
apt-get install libusb-dev joystick python-pygame bluetooth.

Potem robota ponovno zaženemo in se po zagonu zopet povežemo nanj preko terminalskega vmesnika, ter zaženemo naslednje ukaze:
bluetoothctl
discoverable on
agent on

Konzolo fizično povežemo z robotom, in ko se na robotu pojavi okno, s katerim nas sprašuje za avtorizacijo povezave s konzolo, kliknemo na možnost Always Accept. Hkrati nam izpiše tudi konzolin MAC naslov, ki si ga moramo zapomniti.

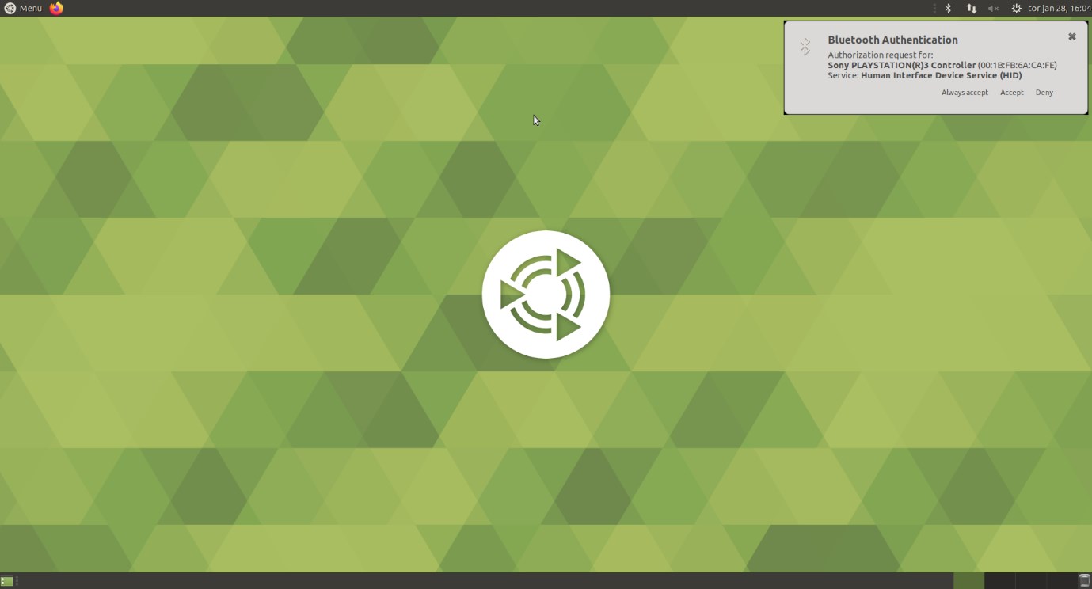
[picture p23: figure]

Ko dovolimo avtorizacijo, konzolo fizično odklopimo z robota, pritisnemo PS tipko in lučke na konzoli začnejo utripati. Na terminalskem vmesniku potem izvedemo ukaza, kjer MAC naslov nadomestimo s tistim, ki naj bi ga sporočil robot:
connect 00:1B:FB:6A:CA:FE
trust 00:1B:FB:6A:CA:FE

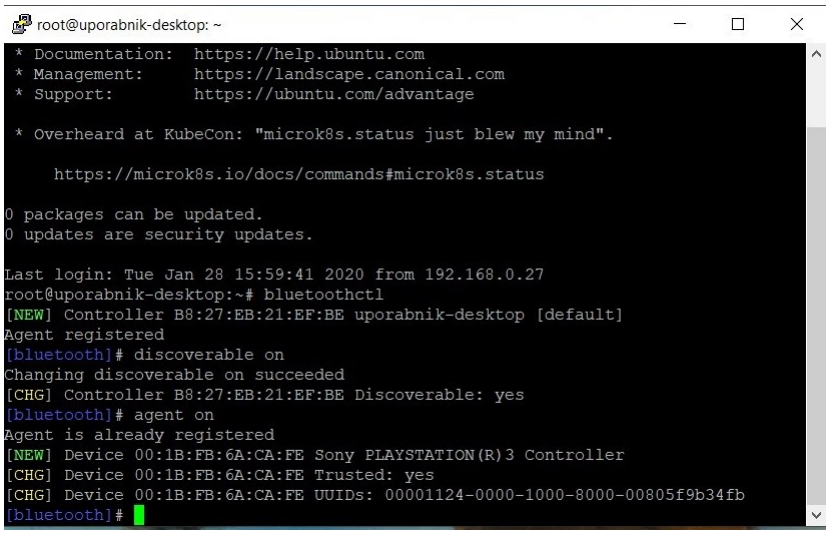
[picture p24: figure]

Če je šlo vse v redu, potem smo uspešno povezali konzolo in robota. Ko bomo v bodoče hoteli robota upravljati s konzolo, bo po zagonu programa potrebno zgolj pritisniti tipko PS na konzoli. Če pa se zgodi, da robot vseeno pozabi na konzolo, je postopek potrebno ponoviti.

Da je konzola res povezana, lahko preverimo na dva načina.

Pri prvem načinu v terminalskem vmesniku robota poženemo ukaz:
ls /dev/input/js*
Če nam izpiše kaj podobnega kot /dev/input/js0, potem je robot povezan s konzolo.

Lahko pa v terminalskem vmesniku robota poženemo ukaz:
jstest /dev/input/js0
in program nam bo sproti izpisoval stanje tipk.

Ko smo povezali robota in konzolo, je potrebno namestiti še ROS ps3joy paket (http://wiki.ros.org/ps3joy), ki preko topica joy sporoča stanje tipk na konzoli v trenutku, ko se stanje spremeni, na primer, ko pritisnemo kako izmed tipk na konzoli. To smo naredili sicer že v navodilih za inštalacijo sisteam pri koraku 9:
apt-get install ros-melodic-joy
apt-get install ros-melodic-joystick-drivers.

Robota upravljamo s konzolo tako, da poženemo ukaz: roslaunch roborodney robot_joy.launch.

POGLED NA ROBOTOVO KAMERO MED UPRAVLJANJEM ROBOTA

Med upravljanjem robota, tako s pomočjo tipkovnice kot tudi s PS3 KONZOLO, lahko preko internetnega brskalnika spremljamo pogled robota preko vgrajene kamere. To dosežemo tako, da v spletni brskalnik vpišemo IP številko robota na portu 8000 (npr. http://192.168.0.45:8000/index.html).


Na takšen način lahko robota vodimo na daljavo, lahko tudi preko VPN povezave z oddaljene lokacije. Hitrost prenosa slike je odvisna od hitrosti internetnih povezav, zato je potrebna previdnost pri vožnji, da se robot ne zaleti v kakšno oviro.

SAMOSTOJNA VOŽNJA ROBOTA

Robot je sposoben tudi osnovne avtonomne navigacije po prostoru. Program za samostojno navigacijo poženemo z ukazom
roslaunch roborodney robot_auto.launch

Na začetku robot določi ciljno smer – to je smer, v katero je obrnjen pri zagonu programa. Robot se potem začne premikati proti ciljni smeri in med samo vožnjo smer popravlja, če zaide preveč levo ali desno. Vožnja poteka toliko časa, dokler robot ne naleti na oviro – takrat se ustavi in pregleda, če je pred njim QR koda. Če naleti na QR kodo, potem poskuša iz kode izluščiti ukaz, ga izvede in nadaljuje vožnjo.

Če ne naleti na QR kodo, potem začne s skeniranjem okolice – pladenj s senzorji obrne v levo za 90 stopinj, ga po korakih premika v desno in na vsakem koraku izmeri razdaljo do ovire. Ko konča, zasuče pladenj v srednjo pozicijo in izračuna, v katero smer mora nadaljevati, da se uspešno izogne oviram. Robot se potem obrne v izračunano smer in nadaljuje vožnjo.

Robot nadaljuje vožnjo toliko časa, dokler na naleti na ukaz STOP. Robota lahko ustavimo tudi tako, da v konzoli, v kateri smo pognali program za samostojno vožnjo, naenkrat pritisnemo tipki CTRL in
C. Program za vožnjo se bo prenehal izvajati. Če prekinitev ne zaleže, ali če izgubimo nadzor, je robota najlažje ugasniti tako, da odklopimo baterije.

Pri vožnji si robot za zaznavanje ovir na poti pomaga s premikanjem pladnja levo in desno. Tako zazna tudi ovire, ki se ne nahajajo zgolj v smeri vožnje, ampak so pomaknjene rahlo levo ali desno in bi ga motile pri vožnji.

Ukazov s QR kodo je trenutno 5:
1. levo za 90 stopinj (LEFT)
2. desno za 90 stopinj (RIGHT)
3. obrat za 180 stopinj (TURN)
4. ustavi delovanje (STOP).

Sam robot bi moral biti sposoben vožnje po prostoru, paziti je potrebno le, da so ovire na njegovi poti višje od 10 cm, drugače jih laser ne zazna in robot se lahko zaleti v njih. Za preizkušanje robota je najbolje najprej postaviti nekaj umetnih ovir ter sprožiti vožnjo, da vidimo, kako se obnaša in če ima pri vožnji kakšne težave.

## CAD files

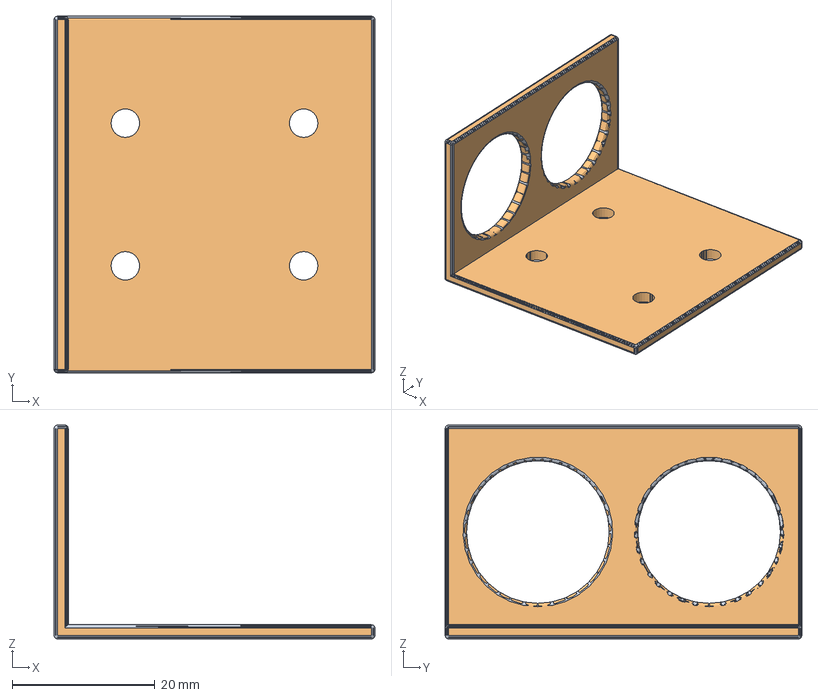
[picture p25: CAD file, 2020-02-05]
Nacrti/FreeCAD/SRF05.FCStd
45.0 x 50.0 x 30.0 mm
Body (Meshed)

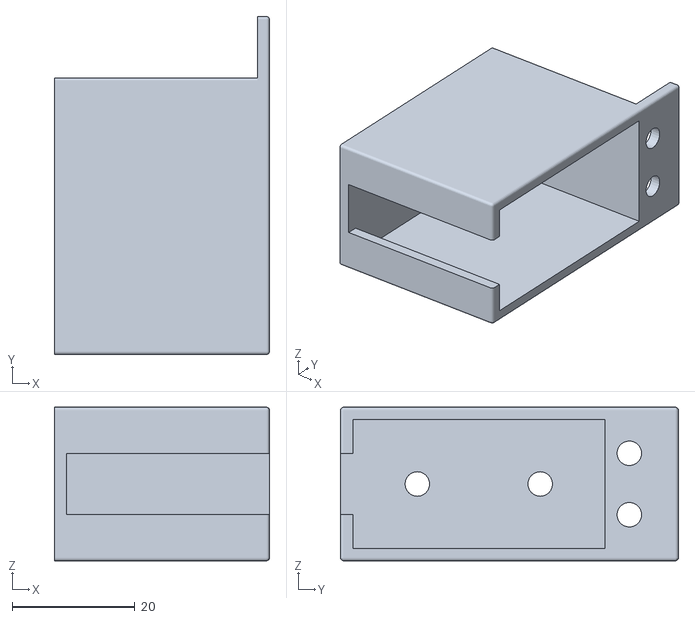
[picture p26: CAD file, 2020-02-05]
Nacrti/stl/NosilecServo.stl
35.0 x 55.0 x 25.0

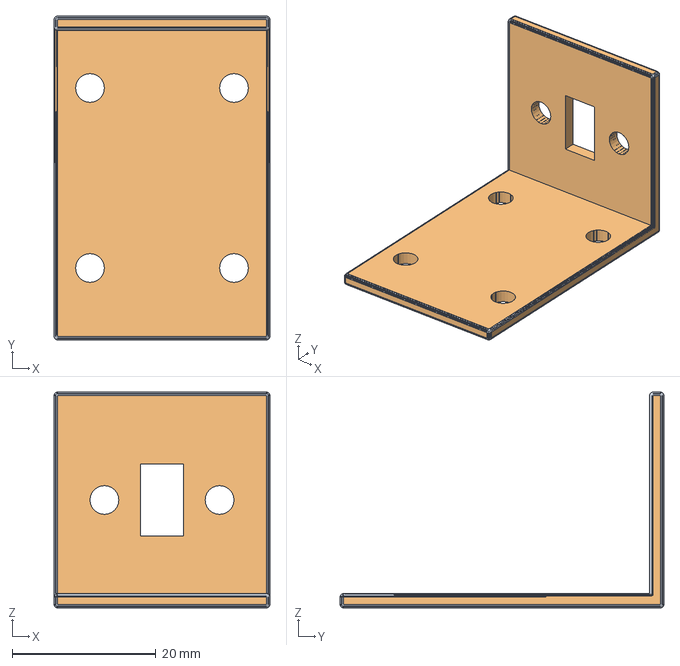
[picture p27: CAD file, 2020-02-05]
Nacrti/FreeCAD/Laser.FCStd
30.0 x 45.0 x 30.0 mm
Body (Meshed)

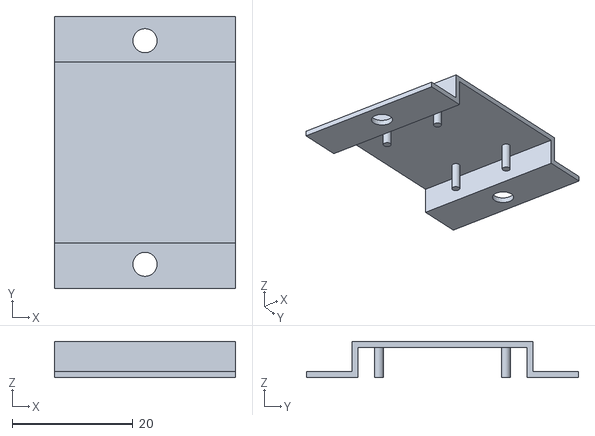
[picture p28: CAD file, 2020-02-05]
Nacrti/stl/NosilecKameraZadnji.stl
30.0 x 45.0 x 6.00

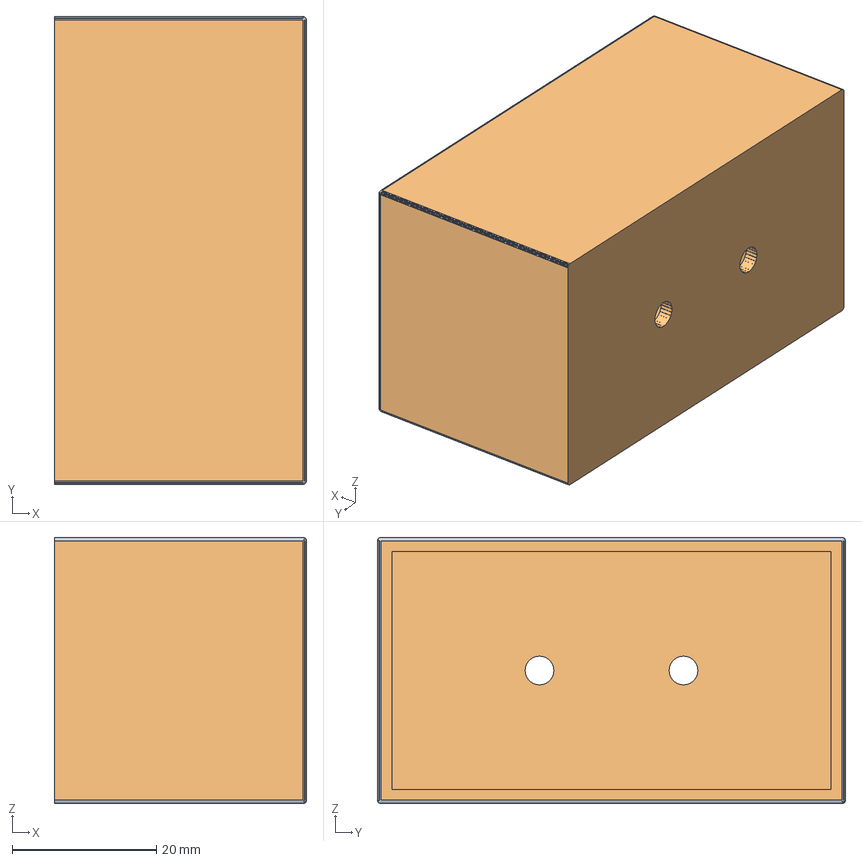
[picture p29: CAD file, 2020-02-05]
Nacrti/FreeCAD/NosilecBaterije8.FCStd
35.0 x 65.0 x 37.0 mm
Body (Meshed)

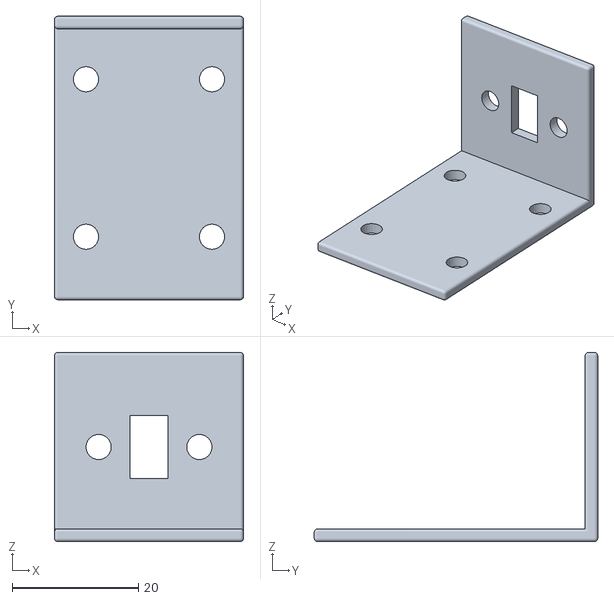
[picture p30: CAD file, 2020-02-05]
Nacrti/stl/NosilecLaser.stl
30.0 x 45.0 x 30.0

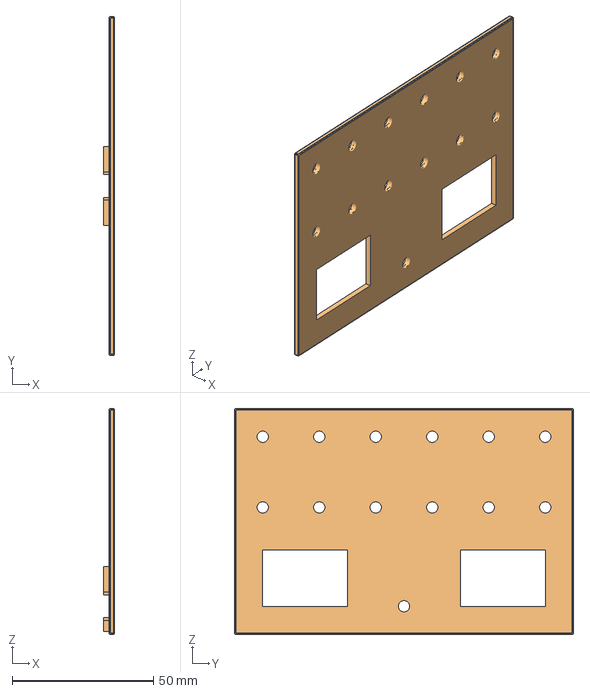
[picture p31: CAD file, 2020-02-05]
Nacrti/FreeCAD/NosilecSenzorji.FCStd
4.00 x 120.0 x 80.0 mm
Body (Meshed)

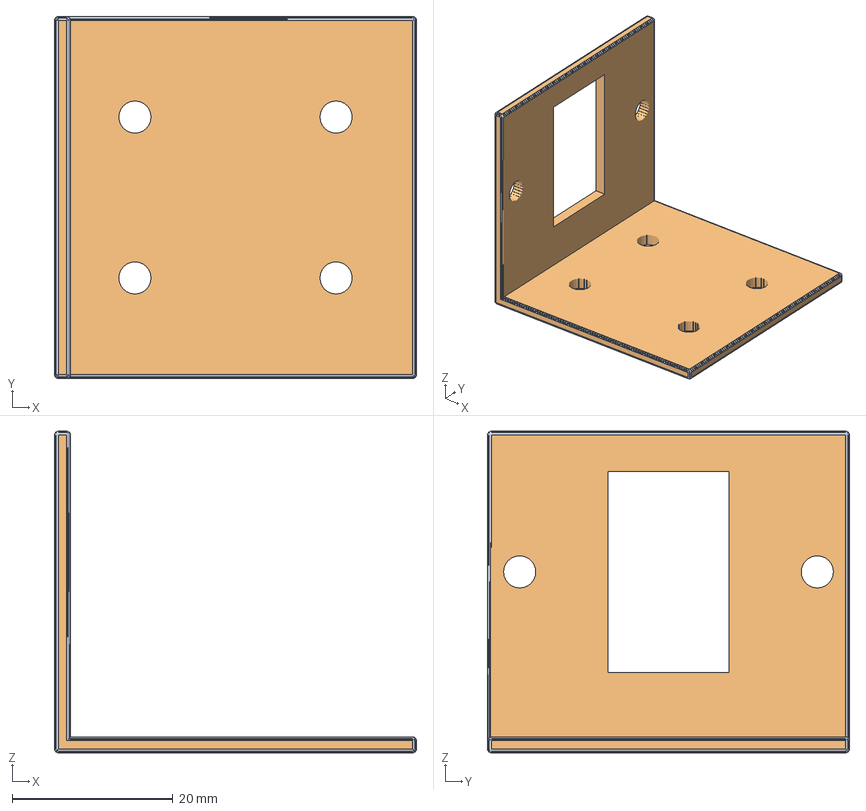
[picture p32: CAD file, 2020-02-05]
Nacrti/FreeCAD/NosilecKameraSprednja.FCStd
45.0 x 45.0 x 40.0 mm
Body (Meshed)

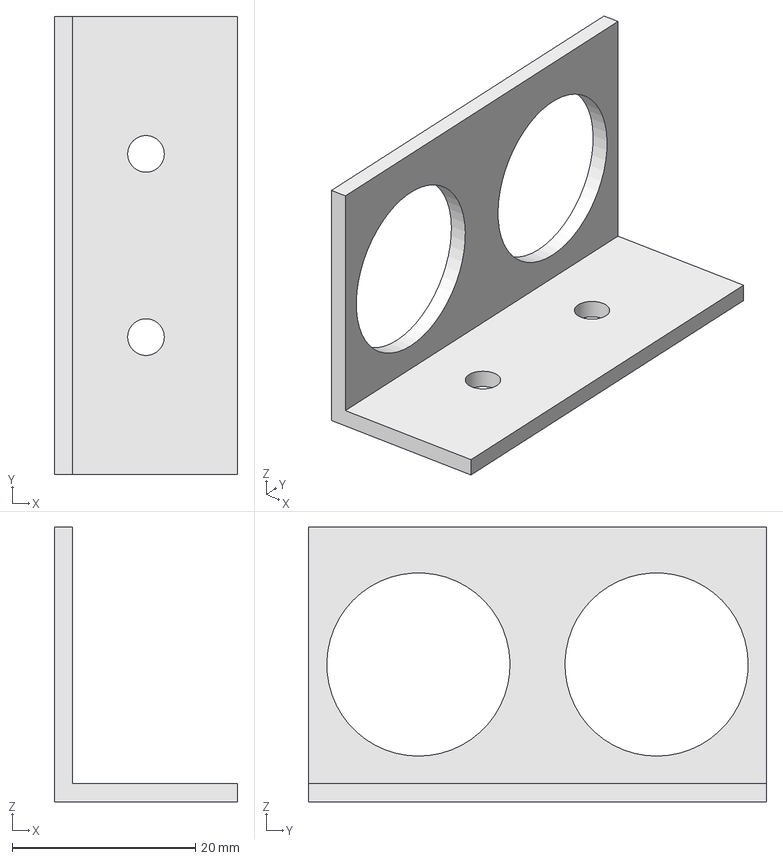
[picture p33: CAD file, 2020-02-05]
Nacrti/FreeCAD/HCSR04.FCStd
20.0 x 50.0 x 30.0 mm

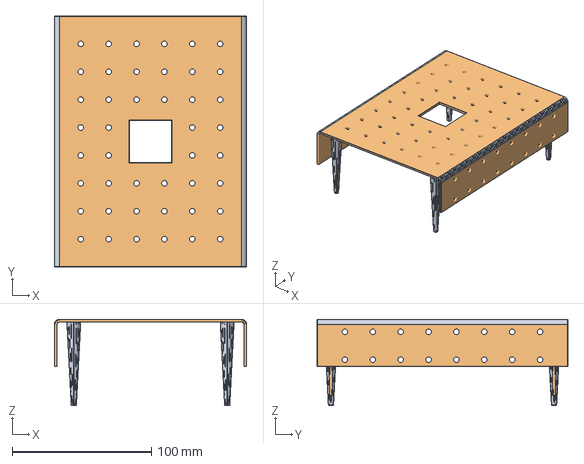
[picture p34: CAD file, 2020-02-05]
Nacrti/FreeCAD/ZgornjaPlast_2mm.FCStd
138.0 x 180.0 x 62.0 mm
Body001 (Meshed)

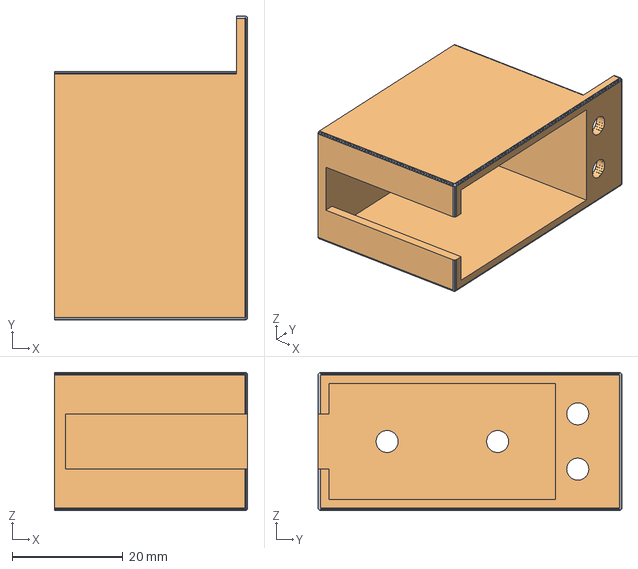
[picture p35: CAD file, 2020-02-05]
Nacrti/FreeCAD/NosilecServoMotor.FCStd
35.0 x 55.0 x 25.0 mm
Body (Meshed)

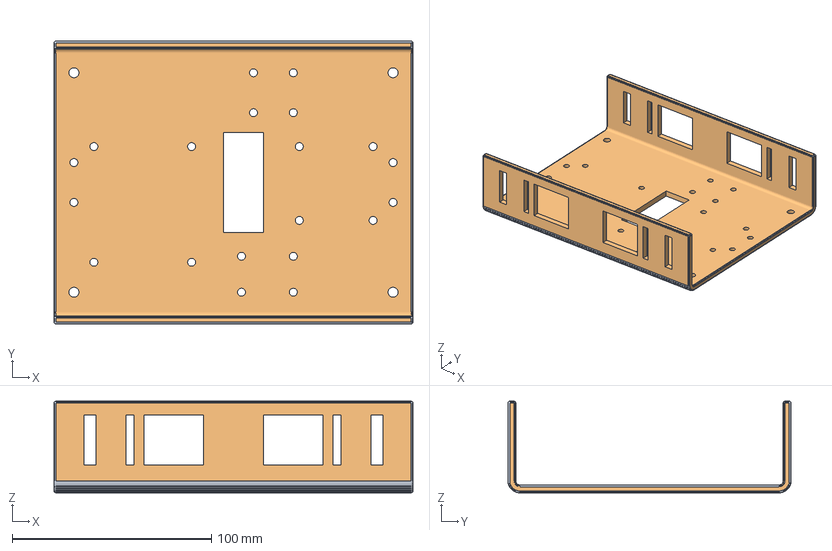
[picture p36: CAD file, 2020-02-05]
Nacrti/FreeCAD/SpodnjaPlast4mm.FCStd
180.0 x 142.0 x 46.0 mm
Body (Meshed)

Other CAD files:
Nacrti/FreeCAD/NosilecKameraZadnja.FCStd
Nacrti/stl/NosilecBaterije8.stl
Nacrti/stl/NosilecKameraSprednja.stl
Nacrti/stl/NosilecSenzorji.stl
Nacrti/stl/SRF05.stl
Nacrti/stl/SpodnjaPlast4mm.stl
Nacrti/stl/ZgornjaPlast2mm.stl

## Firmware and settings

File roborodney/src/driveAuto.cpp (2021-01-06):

#include <ros/ros.h>
#include <string>
#include <iostream>
#include <stdio.h>
#include <termios.h>
#include <fstream>
#include <sensor_msgs/Imu.h>
#include <opencv2/highgui/highgui.hpp>
#include <opencv2/imgproc/imgproc.hpp>
#include <std_msgs/String.h>

#include "roborodney/sensorDistance.h"
#include "roborodney/drivingCommand.h"
#include "roborodney/pointsSurroundScan.h"
#include "roborodney/facePosition.h"
#include "roborodney/servoPosition.h"

using namespace cv;
using namespace std;

//global publishers and subscribers 
ros::Publisher trayLeftRight;
ros::Publisher surroundScanCommand;
ros::Publisher driving_command;

// global variables
int locked=0;
int scanInProgress=0;
//variable for distance measurement to obstacle
float currentDistance=0; 
float currentAngle=0;
string direction="stop";
//variable for goal angle
float goalAngle=0;
//variable that count moves for checking, if robot is going to right direction
int forwardStepCounter=0;

//variables for controlling events 
int startOfDrive=1;
int scannedQR=0;  //
int scannedSurround=0; //ce je skeniral okolico
int turnedRobot=0;
int angleOfRotation=0;
int driveInProgress=0;

//variables that tells if robot has recently detected QR code or face
string qrCodeCommand="";
int encounteredAnObstacle=0;
int encounteredAnQrCode=0;
double xx1,xx2,yy1,yy2, resx, resy, xCentre, xCentreOfPicture; 
bool detectedFace=false; 

//min and max of scurity distance in cm - obstacle lies between these two values
int maxSecurityDistance=30; 
int minSecurityDistance=5;

//for sending driving commands - forward, backward, left, right
roborodney::drivingCommand directionCommand;

//for surroundings scan - used in getEnvironmentalPoints function
cv::Mat matrix(400,400,CV_8UC1,cv::Scalar(255));
cv::Mat matrixWeight(400,400,CV_8UC1,cv::Scalar(255));
cv::Mat matrixWeightInv(400,400,CV_8UC1,cv::Scalar(255));
std::vector<float>anglesOnGraph;
std::vector<float>valuesOnGraph;
int numberOfAnglesOnGraph = 19;
std::vector<Mat> weightOnMatrix;
vector<geometry_msgs::Point> Points;
vector<float>distancesScan;

//-----------------------------------------------------------------------------------------------------------------
//function that rotates robot for desired angle
void robotRotation(int angle)
{
	ros::Rate secondDelay(1);
	ros::Rate tenthOfSecondDelay(10); 
	ros::Rate hundredthsOfSecondDelay(100);
	
	ros::spinOnce();
	tenthOfSecondDelay.sleep();
	ros::spinOnce();
	
	float startAngle = currentAngle;
	float endAngle = 0;
	float safetyAngle=0; //user can manualy set angle, that robot doesn't turn too much on one side
	int numberOfSteps=0;
	
	directionCommand.speed=50; 
	directionCommand.duration=20;  
	
	while(angle>=360){angle=angle-360;}
	while(angle<=-360){angle=angle+360;}
	
	if(angle>180){angle=angle-180;}
	if(angle<-180){angle=angle+180;} 
	
	if(angle > 0)
	{
		endAngle = currentAngle+angle-safetyAngle;
		if(endAngle>180){endAngle=endAngle-360;}
		if(endAngle>178){endAngle=178;}
		
		if(startAngle>endAngle)
		{
			while(currentAngle>0){
				directionCommand.direction="left";
				driving_command.publish(directionCommand);
				numberOfSteps++;
				ros::spinOnce();
				for(int i=0;i<3;i++){ros::spinOnce();hundredthsOfSecondDelay.sleep();} 
				ros::spinOnce();
				hundredthsOfSecondDelay.sleep();
			}
		}
		
		while(currentAngle<endAngle)
		{
			directionCommand.direction="left";
			driving_command.publish(directionCommand);
			numberOfSteps++;
			ros::spinOnce();
			for(int i=0;i<3;i++){ros::spinOnce();hundredthsOfSecondDelay.sleep();}
			ros::spinOnce();
			hundredthsOfSecondDelay.sleep();
		}
	} else 
	{
		endAngle = currentAngle+angle+safetyAngle;
		if(endAngle<-180){endAngle=endAngle+360;} 
		if(endAngle<-178){endAngle=-178;}
		
		if(startAngle<endAngle)
		{
			while(currentAngle<0){
				directionCommand.direction="right";
				driving_command.publish(directionCommand);
				numberOfSteps++;
				ros::spinOnce();
				for(int i=0;i<3;i++){ros::spinOnce();hundredthsOfSecondDelay.sleep();}
				ros::spinOnce();
				hundredthsOfSecondDelay.sleep();
			}
		}
		
		while(currentAngle>endAngle)
		{
			directionCommand.direction="right";
			driving_command.publish(directionCommand);
			numberOfSteps++;
			ros::spinOnce();
			for(int i=0;i<3;i++){ros::spinOnce();hundredthsOfSecondDelay.sleep();}
			ros::spinOnce();
			hundredthsOfSecondDelay.sleep();
		}
	}
}
//-----------------------------------------------------------------------------------------------------------------

//-----------------------------------------------------------------------------------------------------------------
//function that gets distance to obstacle that is measured with laser
//when robots gets value for obstacle, that is between boudaries, tray and robot is 
void getSensorDistance(const roborodney::sensorDistance& msg)
{
	currentDistance = msg.distance;
	std_msgs::String msgg;
	if(msg.distance>minSecurityDistance && msg.distance<maxSecurityDistance && locked==0 && scanInProgress==0)
	{
		encounteredAnObstacle=1;
		msgg.data="stop";
		trayLeftRight.publish(msgg);
	}
}
//-----------------------------------------------------------------------------------------------------------------

//-----------------------------------------------------------------------------------------------------------------
//function, that gets detected QR code
void getQrCommand(const std_msgs::String& msg){ 
	encounteredAnQrCode=1;
	
	if(msg.data=="LEFT"){

		qrCodeCommand="LEFT";
	}
	if(msg.data=="RIGHT"){

		qrCodeCommand="RIGHT";
	}
	if(msg.data=="TURN"){

		qrCodeCommand="TURN";
	}
	if(msg.data=="CONTINUE"){

		qrCodeCommand="CONTINUE";
	}
	if(msg.data=="STOP"){

		qrCodeCommand="STOP";
	}	
}
//-----------------------------------------------------------------------------------------------------------------

//-----------------------------------------------------------------------------------------------------------------
//function, that gets points from surroundings scan nd with VFH algorithm calculates directon to avoid obstacles
void gerEnvironmentalPoints(const roborodney::pointsSurroundScan& msg)
{
	ros::Rate tenthOfSecondDelay(10);
	
	anglesOnGraph.clear();
	valuesOnGraph.clear();
	weightOnMatrix.clear();
	Points.clear();
	distancesScan.clear();

	scanInProgress=0;

	//loop that creates matrix with wich calculates right direction
	//kartezis histogram
	matrix = cv::Scalar(255);
	matrixWeight = cv::Scalar(255);
	matrixWeightInv = cv::Scalar(255);
	for(int i=0;i<Points.size();i++) {
		if(Points[i].x<200 && Points[i].x>-200 && Points[i].y<200 && Points[i].y>5) {
			int x=(int)(Points[i].x+200); 
			int y=(int)(400-Points[i].y);
			matrix.at<uchar>(y,x)=0;
			int distanceWeights=(fabs(100-distancesScan[i])/100)*30;
			matrixWeight.col(x).row(y)=matrixWeight.col(x).row(y)-15;
			for(int j=x-1; j<=x+1; j++){
				for(int k=y-1;k<=y+1; k++){
					matrixWeight.col(j).row(k)=matrixWeight.col(j).row(k)-distanceWeights;
				}
			}
			for(int j=x-2; j<=x+2; j++){
				for(int k=y-2;k<=y+2; k++){
					matrixWeight.col(j).row(k)=matrixWeight.col(j).row(k)-distanceWeights;
				}
			}
			for(int j=x-3; j<=x+3; j++){
				for(int k=y-3;k<=y+3; k++){
					matrixWeight.col(j).row(k)=matrixWeight.col(j).row(k)-distanceWeights;
				}
			}
			for(int j=x-4; j<=x+4; j++){
				for(int k=y-4;k<=y+4; k++){
					matrixWeight.col(j).row(k)=matrixWeight.col(j).row(k)-distanceWeights;
				}
			}
		}
	}

	//loop that creates negative of matrix - for easier calculation of direction
	for(int i=0;i<400;i++){
		for(int j=0;j<400;j++){
			matrixWeightInv.row(i).col(j) = 255-matrixWeight.row(i).col(j);
		}
	}
	
	
	//Tukaj imam inverzno matriko z utezmi. Sedaj bi moral kopije, 18, spraviti v vector 
	//loop creates apropriate copies of matrix to calculate the value of each section separately
	std::vector<float>radiani;
	for(int i=0;i<numberOfAnglesOnGraph;i++){
		Mat temp;
		matrixWeightInv.copyTo(temp);
		weightOnMatrix.push_back(temp);
		radiani.push_back(i*180/((float)numberOfAnglesOnGraph)*(M_PI/180));
	}
	
	
	//for each of matrix loop sets area
	Mat matrixWeightInvLines;
	matrixWeightInv.copyTo(matrixWeightInvLines);
	vector <float>exYi;
	vector <float>Yi;
	vector <float>YiMax;
	exYi.clear();	
	Yi.clear();
	for(int i=0;i<weightOnMatrix.size();i++){
		exYi.push_back(0);
		YiMax.push_back(0);
	}
	
	//loop that creates all images to calculate values 
	for(int i=0;i<200;i++){
		exYi=Yi;
		Yi.clear();
		for(int j=0;j<weightOnMatrix.size();j++){
			float yPoint=tan(radiani[j])*i;
			Yi.push_back(yPoint);
			if(fabs(Yi[j])>YiMax[j]&&fabs(Yi[j])<399){YiMax[j]=fabs(Yi[j]);}
		}
		Yi.push_back(0);
		
		
		for(int j=0;j<fabs(weightOnMatrix.size()/2);j++){
			if(Yi[j]<399 && Yi[j]>-399){
				matrixWeightInvLines.col(200-i).row(399-fabs(Yi[j]))=255;
				matrixWeightInvLines.col(199+i).row(399-fabs(Yi[j]))=255;
				weightOnMatrix[j].colRange(0,200-i).row(399-fabs(Yi[j]))=0;
				weightOnMatrix[numberOfAnglesOnGraph-1-j].colRange(199+i,399).row(399-fabs(Yi[j]))=0;
				for(int k=fabs(exYi[j])+1;k<fabs(Yi[j]);k++) {
					matrixWeightInvLines.col(200-i).row(399-k)=255;
					matrixWeightInvLines.col(199+i).row(399-k)=255;
					weightOnMatrix[j].colRange(0,200-i).row(399-k)=0;
					weightOnMatrix[numberOfAnglesOnGraph-1-j].colRange(199+i,399).row(399-k)=0;
				}
				if(Yi[j+1]<399 && Yi[j+1]>-399){
					weightOnMatrix[j].colRange(200-i,399).row(399-fabs(Yi[j+1]))=0;
					weightOnMatrix[numberOfAnglesOnGraph-1-j].colRange(0,199+i).row(399-fabs(Yi[j+1]))=0;
					for(int k=fabs(exYi[j+1])+1;k<fabs(Yi[j+1]);k++) {
						weightOnMatrix[j].colRange(200-i,399).row(399-k)=0;
						weightOnMatrix[numberOfAnglesOnGraph-1-j].colRange(0,199+i).row(399-k)=0;
					}
				}
			}
		}
		
		int j = fabs(weightOnMatrix.size()/2);
		if(Yi[j]<399 && Yi[j]>-399){
			matrixWeightInvLines.col(200-i).row(399-fabs(Yi[j]))=255;
			matrixWeightInvLines.col(199+i).row(399-fabs(Yi[j]))=255;
			weightOnMatrix[j].colRange(0,200-i).row(399-fabs(Yi[j]))=0;
			for(int k=fabs(exYi[j])+1;k<fabs(Yi[j]);k++) {
				matrixWeightInvLines.col(200-i).row(399-k)=255;
				matrixWeightInvLines.col(199+i).row(399-k)=255;
				weightOnMatrix[j].colRange(0,200-i).row(399-k)=0;
			}
			if(Yi[j+1]<399 && Yi[j+1]>-399){
				weightOnMatrix[j].colRange(200+i,399).row(399-fabs(Yi[j+1]))=0;
				for(int k=fabs(exYi[j+1])+1;k<fabs(Yi[j+1]);k++) {
					weightOnMatrix[j].colRange(200+i,399).row(399-k)=0;
				}
			}
		}
	}

	//a loop that erases the top of the image for proper calculations
	for(int j=0;j<fabs(weightOnMatrix.size()/2);j++){
		weightOnMatrix[j].colRange(0,399).rowRange(0, 399-YiMax[j+1])=0;
		weightOnMatrix[numberOfAnglesOnGraph-1-j].colRange(0,399).rowRange(0, 399-YiMax[numberOfAnglesOnGraph-1-j])=0;
	}
	int j = fabs(weightOnMatrix.size()/2);
	weightOnMatrix[j].colRange(0,399).rowRange(0, 399-YiMax[j])=0;
	
	//loop that calculates angle and value in hat direction
	//https://stackoverflow.com/questions/21874774/sum-of-elements-in-a-matrix-in-opencv
	anglesOnGraph.clear();
	valuesOnGraph.clear();
	for(int i=0;i<weightOnMatrix.size();i++){
		anglesOnGraph.push_back(i*(180.0/weightOnMatrix.size()));
		valuesOnGraph.push_back(sum(weightOnMatrix[i])[0]);
	}
	
	//loop gets direction with smallest value to turn the robot in that direction
	float minimum=100000;
	int position=0;
	for(int i=4;i<anglesOnGraph.size()-4;i++){
		float currentValue = (0.5*valuesOnGraph[i-1])+(2*valuesOnGraph[i])+(0.5*valuesOnGraph[i+1]);
		if(minimum>currentValue){
			minimum=currentValue;
			position=i;
		}
	}
	
	//sets direction for robot to continue
	float shiftAngle = 90 - (((anglesOnGraph[position+1]-anglesOnGraph[position])/2)+anglesOnGraph[position]);
	angleOfRotation=int(shiftAngle);
	locked=0;		
}
//-----------------------------------------------------------------------------------------------------------------

//-----------------------------------------------------------------------------------------------------------------
//function gets position on a plane from BNO055 senzor in quaternion and calculates angle on 2D plane (yaw) and also alerts if BNO055 sensor doesn't send data
void getAngleOnPlane(const sensor_msgs::Imu& msg)
{
	ros::Rate secondDelay(1);
	
	//racunam se yaw
	double siny_cosp = +2.0 * (msg.orientation.w * msg.orientation.z + msg.orientation.x * msg.orientation.y);
	double cosy_cosp = +1.0 - 2.0 * (msg.orientation.y * msg.orientation.y + msg.orientation.z * msg.orientation.z);
	double kot = atan2(siny_cosp, cosy_cosp);
	double kotkot = (kot*180)/3.14;
	currentAngle=kotkot;
	
	if(isnan(msg.orientation.x)){
		ROS_INFO("BNO055 DOWN!!!!");
		secondDelay.sleep();
		secondDelay.sleep();
		secondDelay.sleep();
	}
	
}
//-----------------------------------------------------------------------------------------------------------------

//-----------------------------------------------------------------------------------------------------------------
//function for display current settings
void displayData() {
	ROS_INFO("Speed: %d  Duration: %d Kot: %f Angle of goal: %f", directionCommand.speed, directionCommand.duration, currentAngle, goalAngle);
}
//-----------------------------------------------------------------------------------------------------------------

//-----------------------------------------------------------------------------------------------------------------
//function that gets position of a detected face from a camera
void functionFacePosition(const roborodney::facePosition& msg)
{
    if (msg.p2.x>0 && msg.p2.y>0) 
    {
        ROS_INFO("Face detection!");
        detectedFace=true;
        xx1=msg.p1.x;
        yy1=msg.p1.y;
        xx2=msg.p2.x;
        yy2=msg.p2.y;     
        resx=msg.res.x;
        resy=msg.res.y;
    }
}


int main(int argc, char **argv)
{
	int counter=0;
	
	ros::init(argc, argv, "driveAuto");
	ros::NodeHandle nh;
	
	ros::Rate secondDelay(1);
	ros::Rate tenthOfSecondDelay(10);
	ros::Rate hundredthsOfSecondDelay(100);
	ros::Rate dvajsetinkasekundePostanek01(20);

	
	driving_command = nh.advertise<roborodney::drivingCommand>("driving_command",10);
	trayLeftRight = nh.advertise<std_msgs::String>("trayLeftRight", 10);
	surroundScanCommand = nh.advertise<std_msgs::String>("surroundScanCommand", 10);
	ros::Subscriber sensorDistance = nh.subscribe("laser_distance", 1, getSensorDistance);
	ros::Subscriber envoronmentPoints = nh.subscribe("surroundPoints", 1, gerEnvironmentalPoints);
	ros::Subscriber angleOnPlane = nh.subscribe("data", 1, getAngleOnPlane);
	ros::Subscriber facePosition = nh.subscribe("facePosition", 1, functionFacePosition);
	ros::Subscriber qrCode = nh.subscribe("barcode", 1, getQrCommand);
	ros::Publisher scannerCommand = nh.advertise<std_msgs::String>("pictureScanCommand", 10);
	
	std_msgs::String msg;
	msg.data="start";
	secondDelay.sleep();
	ros::spinOnce();
	
	directionCommand.direction=direction;
	directionCommand.speed=30;
	directionCommand.duration=20;

	secondDelay.sleep();
	ros::spinOnce();
	
 
	ROS_INFO("Robot is running.");
	
	goalAngle=currentAngle;
	
	int c=0;


	//loop that repeats as long as STOP qr code is not detected or program is not terminated with CTRL-C	
	while(nh.ok()){
		
		//this while statement is executed while surround scan
		while(scanInProgress==1){
			ROS_INFO("Surroundings scan in progress");
			ros::spinOnce();
			secondDelay.sleep();
		} 
		
		ros::spinOnce();
		
		//this if statement starts drive under certain conditions
		if(encounteredAnQrCode==0 && encounteredAnObstacle==0 && driveInProgress==0){	
			scannedQR=0;
			driveInProgress=1;
			ROS_INFO("Tray is moving.");
			msg.data="start";
			trayLeftRight.publish(msg);
			//Robot waits 2 seconds and then begins with driving
			for(int i=0;i<2;i++){ros::spinOnce();secondDelay.sleep();}
			ROS_INFO("Start driving.");
		}
		
		//this if statement is exectued if robot is driving
		if(encounteredAnQrCode==0 && encounteredAnObstacle==0 && driveInProgress==1){
			directionCommand.direction="forward";
			directionCommand.speed=20;
			directionCommand.duration=20;
			driving_command.publish(directionCommand);
			ros::spinOnce();
			hundredthsOfSecondDelay.sleep();
			forwardStepCounter++;
			//this if statement is executed if robot makes 300 moves while driving to check if direction is proper
			if(forwardStepCounter==300){
				ROS_INFO("Checking the driving angle.");
				ROS_INFO("Curent angle %f",currentAngle);
				ROS_INFO("Target angle %f", goalAngle);
				
				//calculates angle for turn
				int newStarting=currentAngle;
				int newEnd=goalAngle;
				int turn=newEnd-newStarting;
				if(turn>180){turn=turn-360;}
				if(turn<-180){turn=turn+360;}

				if(abs(turn)>2){
					ROS_INFO("Turning in the target angle.");
					for(int i=0;i<2;i++){ros::spinOnce();secondDelay.sleep();}
					robotRotation(turn);
					for(int i=0;i<2;i++){
						ros::spinOnce();
						secondDelay.sleep();
					}
					msg.data="start";
					trayLeftRight.publish(msg);
					//Robot waits 2 seconds and then begins with driving
					for(int i=0;i<2;i++){ros::spinOnce();secondDelay.sleep();}
				}
				forwardStepCounter=0;
				encounteredAnObstacle=0;
				driveInProgress==0;
			}
			continue;
			ROS_INFO("Continue driving.");
		}
		
		//this statement is executed if robot encounters obstacle
		if(encounteredAnObstacle==1){
			ROS_INFO("Ran into an obstacle.");
			driveInProgress=0;
			msg.data="stop";
			trayLeftRight.publish(msg);
			ros::spinOnce();
			hundredthsOfSecondDelay.sleep();
			//this if statement is executed if robot encounters obstacle and did not check for QR code yet
			if(scannedQR==0){
				ROS_INFO("Scanning for a QR code");
				msg.data="qrDetection";
				scannerCommand.publish(msg);
				//Robot waits 5 seconds for QR code
				for(int counter=0;counter<5;counter++){
					ros::spinOnce();
					secondDelay.sleep();
				}
				//this if sttatement executes if QR code is detected
				if(encounteredAnQrCode==1){
					if(qrCodeCommand=="STOP"){
						ROS_INFO("Found QR code STOP.");
						exit(0);
					}
					if(qrCodeCommand=="LEFT"){
						ROS_INFO("Found QR code LEFT");
						ROS_INFO("Current target angle %f",goalAngle);
						robotRotation(90);
						encounteredAnObstacle=0;
						goalAngle=goalAngle+90;
						if(goalAngle>180){goalAngle=goalAngle-360;}
						ROS_INFO("New target angle %f",goalAngle);
					}
					if(qrCodeCommand=="RIGHT"){
						ROS_INFO("Found QR code RIGHT");
						ROS_INFO("Current target angle %f",goalAngle);
						robotRotation(-90);
						encounteredAnObstacle=0;
						goalAngle=goalAngle-90;
						if(goalAngle<-180){goalAngle=goalAngle+360;}
						ROS_INFO("New target angle %f",goalAngle);
					}
					if(qrCodeCommand=="TURN"){
						ROS_INFO("Found QR code TURN");
						ROS_INFO("Current target angle %f",goalAngle);
						robotRotation(180);
						encounteredAnObstacle=0;
						goalAngle=goalAngle+180;
						if(goalAngle>180){goalAngle=goalAngle-360;}
						ROS_INFO("New target angle %f",goalAngle);
					} 
					encounteredAnQrCode=0;
					forwardStepCounter=0;
				}
				scannedQR=1; 
				continue;
			}
			
			//tihs if statement is executed if robot stops for obstacle and QR code is not detected - than scans the surroundings
			if(scannedSurround==0){
					ROS_INFO("Scanning the surroundings");
					msg.data="start";
					surroundScanCommand.publish(msg);
					scannedSurround=1;
					scanInProgress=1;
					ros::spinOnce();
					secondDelay.sleep();
					continue;
			} else {
				//after scans the surroundings robot turn for calculated angle
				if(turnedRobot==0){
					ROS_INFO("Turnig the robot for angle %d",angleOfRotation);
					robotRotation(angleOfRotation);
					scannedQR=0;
					turnedRobot=1;
					forwardStepCounter=0;
					secondDelay.sleep();
				} else {
					//this part executes after robot turns for ceratin angle to avoid obstacle
					turnedRobot=0;
					encounteredAnObstacle=0;
					scannedSurround=0;
					continue;
				}
			}
		}
		ros::spinOnce();		
	}
	ROS_INFO("Terminating the program.");
	return 0;
}

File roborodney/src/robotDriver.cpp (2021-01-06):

#include <ros/ros.h>
#include <wiringPi.h>
#include <softPwm.h>
#include <stdio.h>
#include <termios.h>
#include "std_msgs/String.h"
#include <string>
#include "roborodney/drivingCommand.h"


// pins on L298N motor driver
// with L298N motor driver can control two DC motors. Pins on 5 and 6 are connected to right motor, nad pins 19 and 13 are connected with left motor
// When we send signal on pin 5 it means, that right motor is spinning forward, and when we send signal on pin 6 it means, thar right motor is spinnig backward
// The same means for pins 19 and 13 for right motor 

int in1 = 5;  //right motor forward
int in2 = 6;  //right motor backward
int in3 = 19;  //left motor forward
int in4 = 13;  //left motor backward

// Next four functions are actually driving robot. They send direction and speed to left and right motor, then wait for a certain period of time, then stop motors.

//moving forward 
void forward(int duration, int speed)
{
  softPwmWrite (in1, speed);  
  softPwmWrite (in3, speed);
  delay(duration);
  softPwmWrite (in1, 0);  
  softPwmWrite (in3, 0);
}

//moving backward
void backward(int duration, int speed)
{
  softPwmWrite (in2, speed);  
  softPwmWrite (in4, speed);
  delay(duration);
  softPwmWrite (in2, 0);  
  softPwmWrite (in4, 0);
}

//rotating left
void left(int duration, int speed)
{
  softPwmWrite (in2, speed);  
  softPwmWrite (in3, speed);
  delay(duration);
  softPwmWrite (in2, 0);  
  softPwmWrite (in3, 0);
  ROS_INFO("SEL LEVO!!!");
}

//rotating right
void right(int duration, int speed)
{
  softPwmWrite (in4, speed);  
  softPwmWrite (in1, speed);
  delay(duration);
  softPwmWrite (in4, 0);  
  softPwmWrite (in1, 0);
}

// This function gets command for direction, speed and duration for driving robot's motors via driving_command topic and then sends apropriate command to one of the four functions above
void getCommand(const roborodney::drivingCommand& msg)
{
  std::string direction = msg.direction.c_str(); //direction of robot
  int speed = msg.speed;  //speed of motors, from 0 (min) to 100 (max) in PWM duty cycle
  int duration = msg.duration; //signal duration in micro seconds

  if (direction.compare("left")==0){ROS_INFO("Going left.");left(duration,speed);}
  if (direction.compare("right")==0){ROS_INFO("Going right.");right(duration,speed);}
  if (direction.compare("forward")==0){ROS_INFO("Going forward.");forward(duration,speed);}
  if (direction.compare("backward")==0){ROS_INFO("Going backward.");backward(duration,speed);}
}

int main(int argc, char **argv)
{
	ros::init(argc, argv, "robot_driver");
	ros::NodeHandle nh;

	ros::Subscriber ukaz_smeri = nh.subscribe("driving_command", 1, getCommand);

	setenv("WIRINGPI_GPIOMEM", "1", 1);

	//Initialisation of L298N motor driver
	wiringPiSetupGpio();
	pinMode(in4,OUTPUT);
	pinMode(in3,OUTPUT);
	pinMode(in2,OUTPUT);
	pinMode(in1,OUTPUT);
	softPwmCreate (in4, 0, 100);
	softPwmCreate (in3, 0, 100);
	softPwmCreate (in2, 0, 100);
	softPwmCreate (in1, 0, 100);

	ros::Duration(1.0).sleep();
	ros::spinOnce();

	printf("Let's drive! \n");
	
	// Program runs until is interrupted by CTRL-C command
	ros::spin();

	printf("Ciao! \n");
	return 0;
}
